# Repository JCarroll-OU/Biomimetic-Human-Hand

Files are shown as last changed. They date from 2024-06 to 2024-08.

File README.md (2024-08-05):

# Biomimetic Human Hand
A mostly 3D-printable 21-DOF biologically inspired robotic human hand prototype.
Joints are actuated via 1mm-diameter 304-Stainless-Steel cable driven by motors in the forearm assembly. These cables are fed through 1mm-ID, 2mm-OD PTFE tubing that runs from the forearm to joints. Additionally, these cables will be driven by N20 motors geared down to 300 RPM.

- **DC Motor Controller PCB** 
  - These PCBs implement a PID control algorithm complete with an auto-tuning feature. Each board can support up to 8 motors, so 4 are required to drive the 21 motors present within this design. Each board is designed to operate at 7-12v.
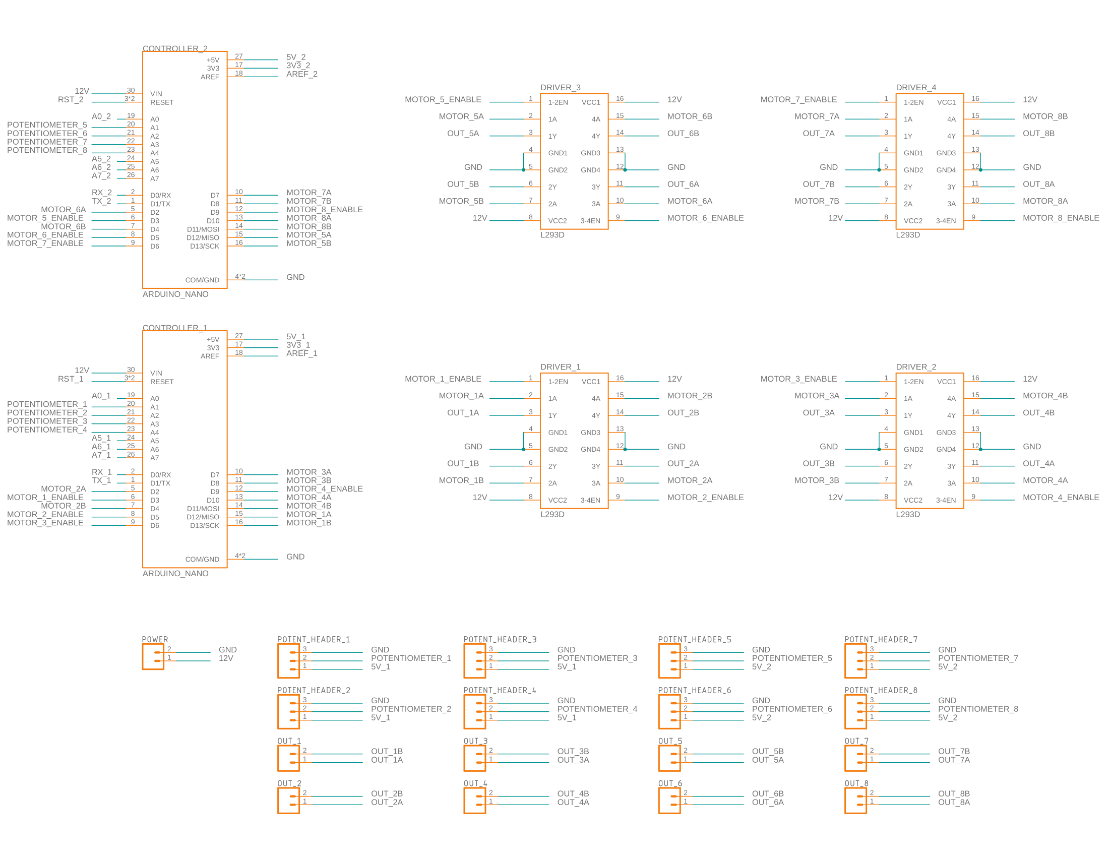
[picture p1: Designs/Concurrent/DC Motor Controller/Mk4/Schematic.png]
Mk. 4 Schematic
  
  - Schematic of Mk. 4 DC Motor Controller PCB. 
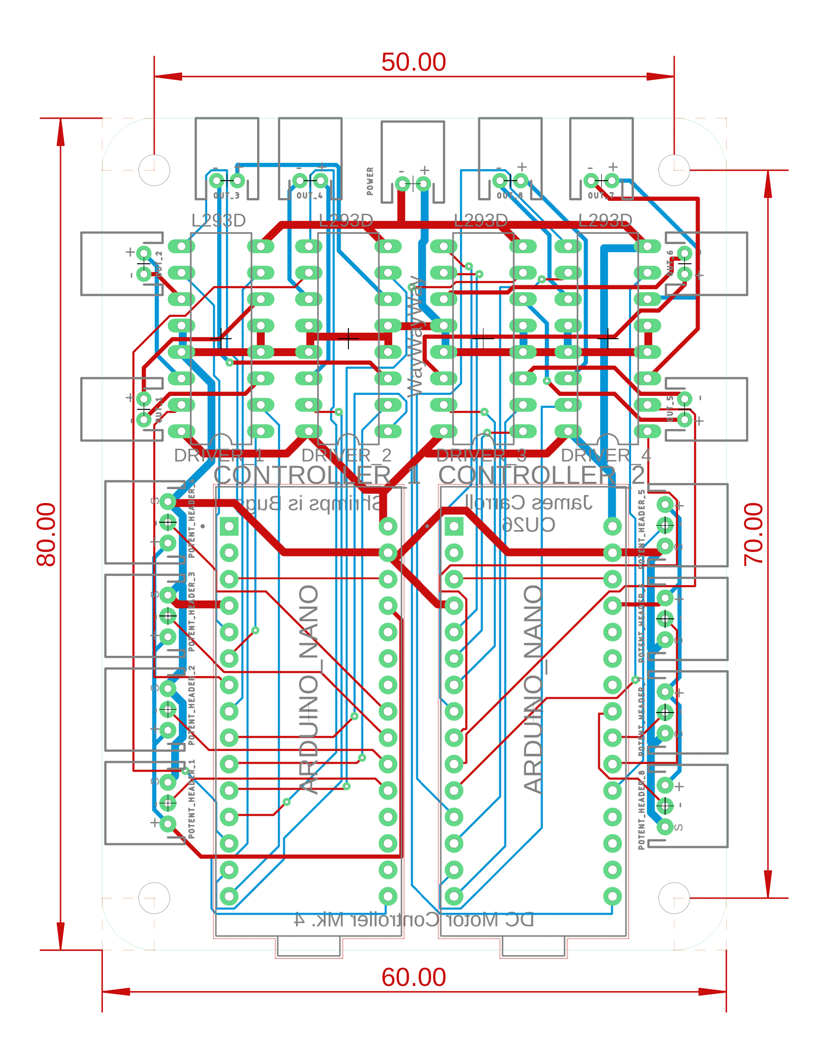
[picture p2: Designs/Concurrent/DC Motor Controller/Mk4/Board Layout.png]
Mk. 4 Board Layout
  
  - PCB Layout and dimensions of Mk. 4 DC Motor Controller PCB. 

- **'Skeletal' System** 
  - Cost was a major design consideration for this prototype. Most parts are designed for 3D-printing (FDM but SLS/SLA is preferrable). Those that are not, are readily available and thus, cheap. 
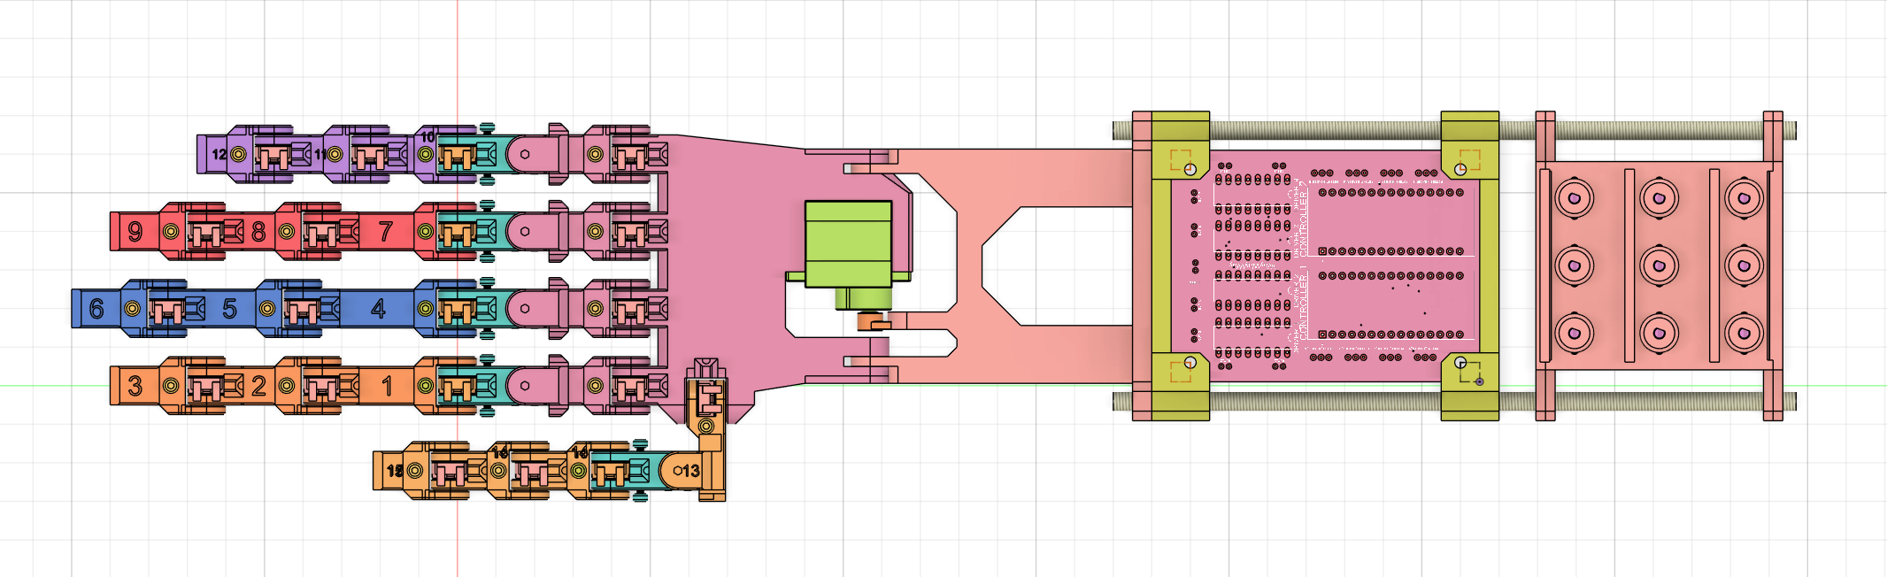
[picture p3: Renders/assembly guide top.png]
WIP: Forearm Assembly, Top
  
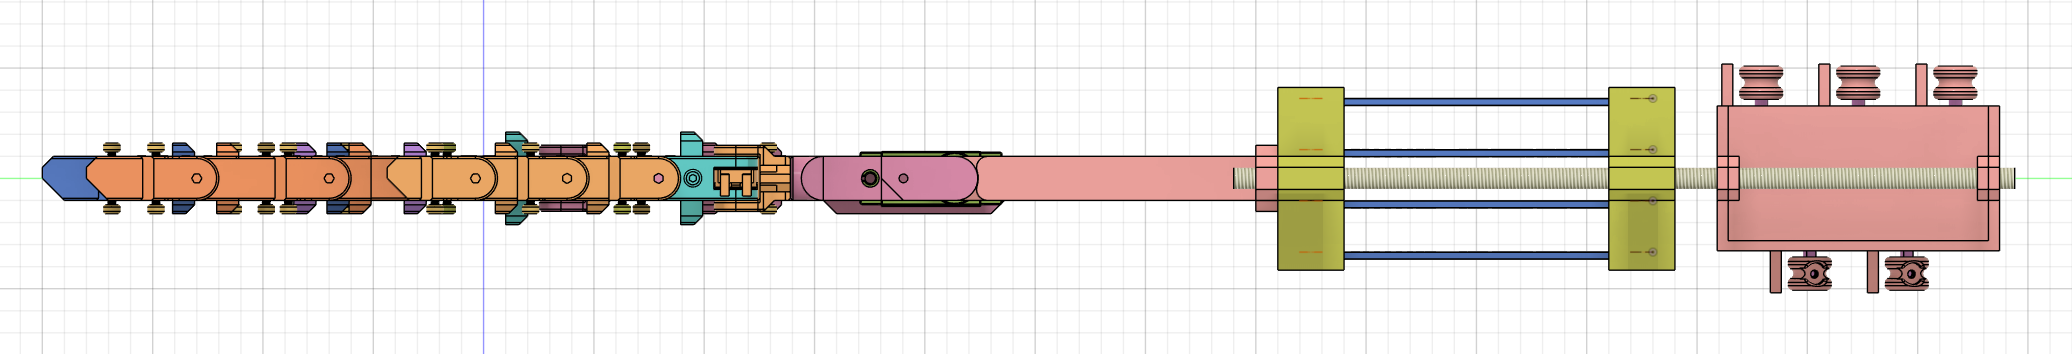
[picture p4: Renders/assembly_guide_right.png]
WIP: Forearm Assembly, Right
  
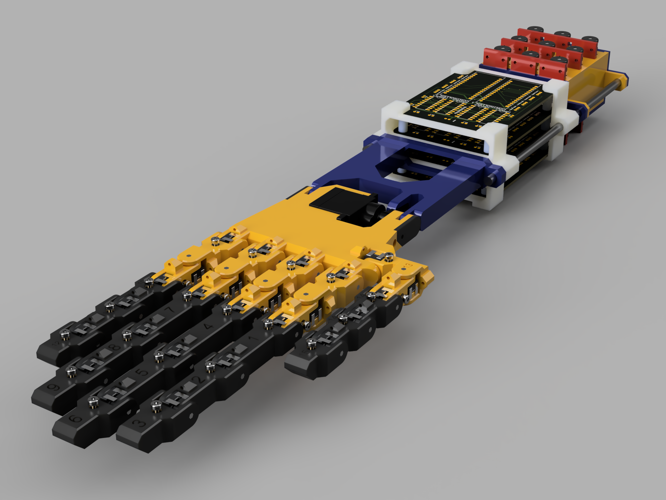
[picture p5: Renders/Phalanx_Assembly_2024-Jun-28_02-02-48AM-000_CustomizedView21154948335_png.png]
WIP: Forearm Assembly, Render
  
  - Finger assemblies in black, palm assembly in yellow, and wrist in blue.
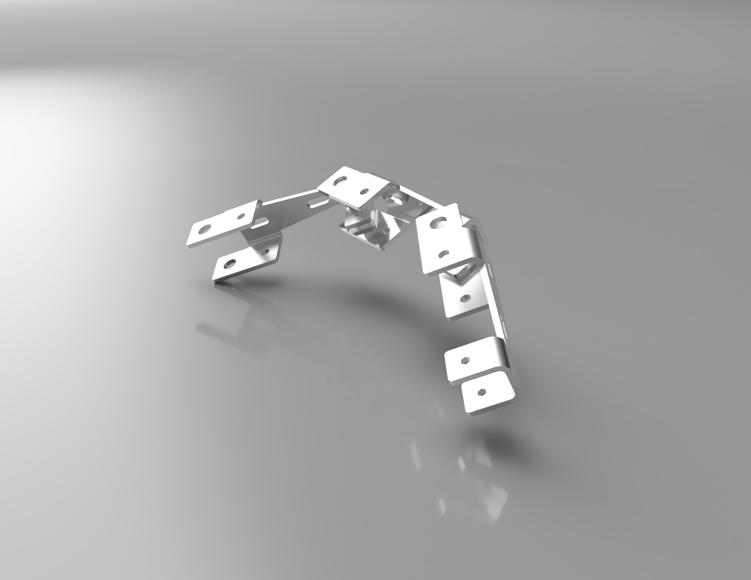
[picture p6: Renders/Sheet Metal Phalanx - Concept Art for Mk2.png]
Concept Art: Production at scale
  
  - Folded sheet metal finger assembly concept art.

  ### This is a work in progress!
  More detailed reports, test results, and notes are available upon request. Contact me or see the license for information regarding the use, reproduction, and distribution of any of the content associated with this project. Thank you!

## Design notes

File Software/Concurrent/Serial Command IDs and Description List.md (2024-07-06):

# Serial Command IDs and descriptions list
  0. SERIAL_CMD_EMPTY
     - Used as part of the handshake protocal. Returns elasped runtime in seconds.
     - Accepts no parameters.
       - Target ID: N/A
       - Param: N/A
     - Example usage:
       - Host: "1 0 0 0.0\n"
         - Controller 1, Command 0, PID 0, 0.0 
       - Client: "13.86\n"
         - Elasped time: 13.86s

  1. SERIAL_CMD_SET_TARGET_ANGLE
     - Sets the 'target angle' variable for the specified PID controller. This is the angle (in degrees) that the PID controller will attempt to move to and hold. 
     - Accepts all parameters
        - Target ID: [1, 4] Int. Values {1, 2, 3, or 4}
          - PID controller to set the target angle of.
        - Param: float [Joint_Range_Min, Joint_Range_Max]
          - New value for the target angle.
     - Example usage:
        - Host: "1 1 2 36.28\n"
          - Controller 1, Command 1, PID 2, 36.28 degrees 
        - Client: "Done\n"

  2. SERIAL_CMD_GET_TARGET_ANGLE
     - Returns the target angle variable for the specified PID controller. 
     - Accepts only the target ID parameter.
        - Target ID: [1, 4] Int. Values {1, 2, 3, or 4}
          - PID controller to get the target angle from.
        - Param: N/A
     - Example usage:
        - Host: "1 2 2 0.0\n"
          - Controller 1, Command 2, PID 2, 0.0 
        - Client: "36.28\n"
          - Target angle: 36.28 degrees

  3. SERIAL_CMD_GET_CURRENT_ANGLE
     - Returns the potentiometer reading (converted to degrees) associated with the specified PID controller.
     - Accepts only the target ID parameter.
        - Target ID: [1, 4] Int. Values {1, 2, 3, or 4}
          - PID controller to get the target angle from.
        - Param: N/A
     - Example usage:
        - Host: "1 3 1 0.0\n"
          - Controller 1, Command 3, PID 1, 0.0 
        - Client: "28.45\n"
          - Current angle: 28.45 degrees

  4. SERIAL_CMD_SET_PID_ENABLE
     - Enables or disables the specified PID controller. Disabling the controller is necessary when manually overriding the motor speed.
     - Accepts all parameters
        - Target ID: [1, 4] Int. Values {1, 2, 3, or 4}
          - PID controller to enable/disable.
        - Param: float, no min/max
          - PID enable state. bool (Param != 0).
     - Example usage:
        - Host: "1 4 3 1.2\n"
          - Controller 1, Command 4, PID 3, 1.2 
        - Client: "Controller_3 enabled\n"
        - Host: "1 4 3 0.0\n"
          - Controller 1, Command 4, PID 3, 0.0
        - Client: "Controller_3 disabled\n"

  5. SERIAL_CMD_GET_PID_ENABLE
     - Returns the state of the specified PID controller.
     - Accepts only the target ID parameter.
        - Target ID: [1, 4] Int. Values {1, 2, 3, or 4}
          - PID controller to get the enable state from.
        - Param: N/A
     - Example usage:
        - Host: "1 5 1 0.0\n"
          - Controller 1, Command 5, PID 1, 0.0 
        - Client: "Enabled\n" or "Disabled\n"

  6. SERIAL_CMD_PID_SET_P
     - Sets the proportional component of the specified PID controller.
     - Accepts all parameters
        - Target ID: [1, 4] Int. Values {1, 2, 3, or 4}
          - PID controller to set the proportional component of.
        - Param: float, no min/max
          - New value for the proportional component.
     - Example usage:
        - Host: "1 6 2 1.86\n"
          - Controller 1, Command 6, PID 2, 1.86 
        - Client: "Done\n"

  7. SERIAL_CMD_PID_GET_P
     - Returns the proportional component of the specified PID controller.
     - Accepts only the target ID parameter.
        - Target ID: [1, 4] Int. Values {1, 2, 3, or 4}
          - PID controller to get the proportional component from.
        - Param: N/A
     - Example usage:
        - Host: "1 7 2 0.0\n"
          - Controller 1, Command 7, PID 2, 0.0 
        - Client: "1.86\n"

  8. SERIAL_CMD_PID_SET_I
     - Sets the integral component of the specified PID controller.
     - Accepts all parameters
        - Target ID: [1, 4] Int. Values {1, 2, 3, or 4}
          - PID controller to set the integral component of.
        - Param: float, no min/max
          - New value for the integral component.
     - Example usage:
        - Host: "1 8 2 1.86\n"
          - Controller 1, Command 8, PID 2, 0.26 
        - Client: "Done\n"

  9. SERIAL_CMD_PID_GET_I
     - Returns the integral component of the specified PID controller.
     - Accepts only the target ID parameter.
        - Target ID: [1, 4] Int. Values {1, 2, 3, or 4}
          - PID controller to get the integral component from.
        - Param: N/A
     - Example usage:
        - Host: "1 9 2 0.0\n"
          - Controller 1, Command 9, PID 2, 0.0 
        - Client: "0.26\n"

  10. SERIAL_CMD_PID_SET_D
      - Sets the derivative component of the specified PID controller.
      - Accepts all parameters
        - Target ID: [1, 4] Int. Values {1, 2, 3, or 4}
          - PID controller to set the derivative component of.
        - Param: float, no min/max
          - New value for the derivative component.
      - Example usage:
        - Host: "1 10 2 0.03\n"
          - Controller 1, Command 8, PID 2, 0.03 
        - Client: "Done\n"

  11. SERIAL_CMD_PID_GET_D
      - Returns the derivative component of the specified PID controller.
      - Accepts only the target ID parameter.
        - Target ID: [1, 4] Int. Values {1, 2, 3, or 4}
          - PID controller to get the derivative component from.
        - Param: N/A
      - Example usage:
        - Host: "1 11 2 0.0\n"
          - Controller 1, Command 11, PID 2, 0.0 
        - Client: "0.03\n"

  12. SERIAL_CMD_SET_ANGLE_CONV_DEG_MIN
      - Sets the minimum bounds for the ADC reading to degrees conversion for the specified PID controller.
      - Accepts all parameters
        - Target ID: [1, 4] Int. Values {1, 2, 3, or 4}
          - PID controller to set the mimimum bounds of.
        - Param: float, no min/max
          - New value for the minimum bounds.
      - Example usage:
        - Host: "1 12 1 24.68\n"
          - Controller 1, Command 12, PID 1, 24.68
        - Client: "Done\n"

  13. SERIAL_CMD_GET_ANGLE_CONV_DEG_MIN
      - Returns the minimum bounds for the ADC reading to degrees conversion for the specified PID controller.
      - Accepts only the target ID parameter.
        - Target ID: [1, 4] Int. Values {1, 2, 3, or 4}
          - PID controller to get the minimum bounds from.
        - Param: N/A
      - Example usage:
        - Host: "1 13 1 0.0\n"
          - Controller 1, Command 13, PID 1, 0.0 
        - Client: "24.68\n"
          
14. SERIAL_CMD_SET_ANGLE_CONV_DEG_MAX
     - Sets the maximum bounds for the ADC reading to degrees conversion for the specified PID controller.
     - Accepts all parameters
        - Target ID: [1, 4] Int. Values {1, 2, 3, or 4}
          - PID controller to set the maximum bounds of.
        - Param: float, no min/max
          - New value for the maximum bounds.
      - Example usage:
        - Host: "1 12 1 76.48\n"
          - Controller 1, Command 14, PID 1, 76.48
        - Client: "Done\n"

  15. SERIAL_CMD_GET_ANGLE_CONV_DEG_MAX
      - Returns the maximum bounds for the ADC reading to degrees conversion for the specified PID controller.
      - Accepts only the target ID parameter.
        - Target ID: [1, 4] Int. Values {1, 2, 3, or 4}
          - PID controller to get the maximum bounds from.
        - Param: N/A
      - Example usage:
        - Host: "1 15 1 0.0\n"
          - Controller 1, Command 15, PID 1, 0.0 
        - Client: "76.48\n"
          
  16. SERIAL_CMD_SET_ANGLE_JOINT_DEG_MIN    
  17. SERIAL_CMD_GET_ANGLE_JOINT_DEG_MIN   
  18. SERIAL_CMD_SET_ANGLE_JOINT_DEG_MAX
  19. SERIAL_CMD_GET_ANGLE_JOINT_DEG_MAX   
          
  20. SERIAL_CMD_SAVE_SETTINGS
  21. SERIAL_CMD_LOAD_SETTINGS

  22. SERIAL_CMD_SET_MOTOR_SPEED
  23. SERIAL_CMD_GET_MOTOR_SPEED
          
  24. SERIAL_CMD_HOMING_SEQUENCE
  25. SERIAL_CMD_PID_AUTOTUNE

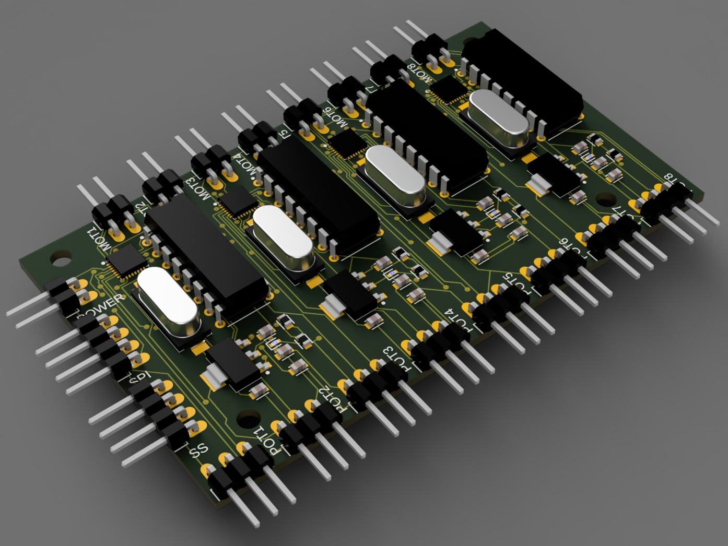
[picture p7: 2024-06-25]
Renders/DC_Motor_Controller_2024-May-17_01-13-07PM-000_CustomizedView9308964263.png

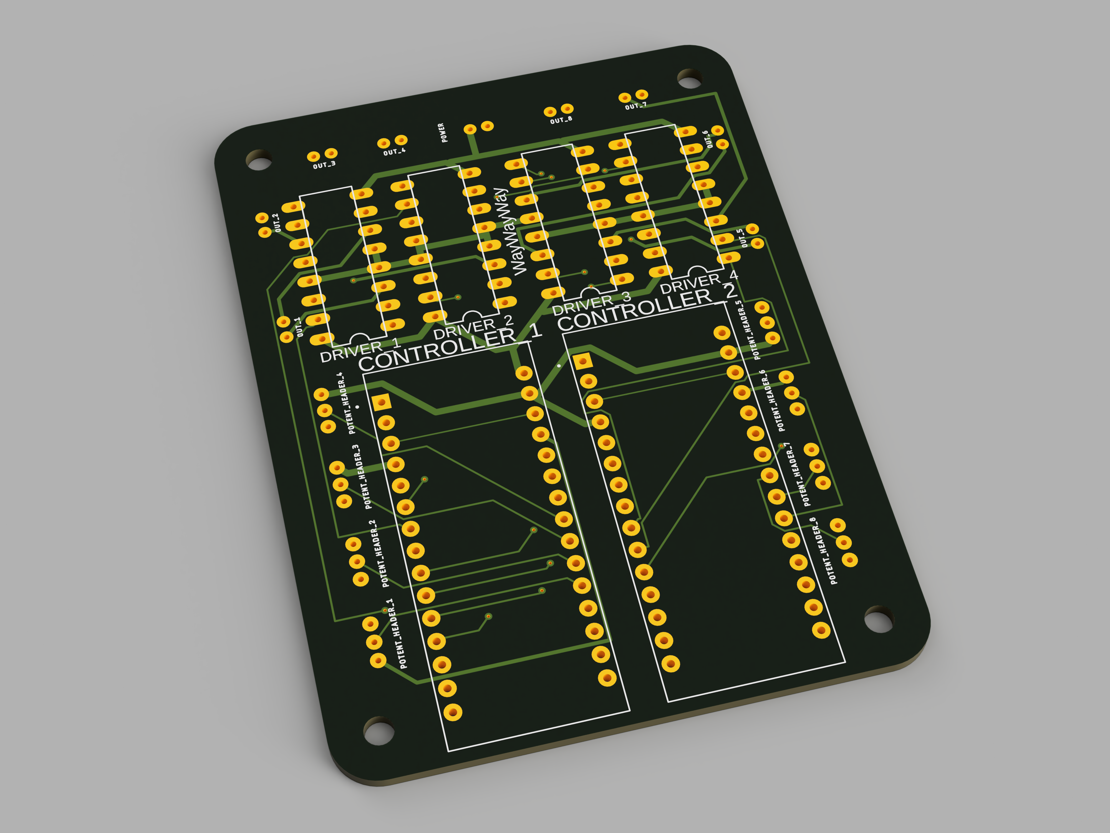
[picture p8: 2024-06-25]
Renders/DC_Motor_Controller_Mk4_2024-Jun-25_07-05-43PM-000_CustomizedView16519912145_png.png

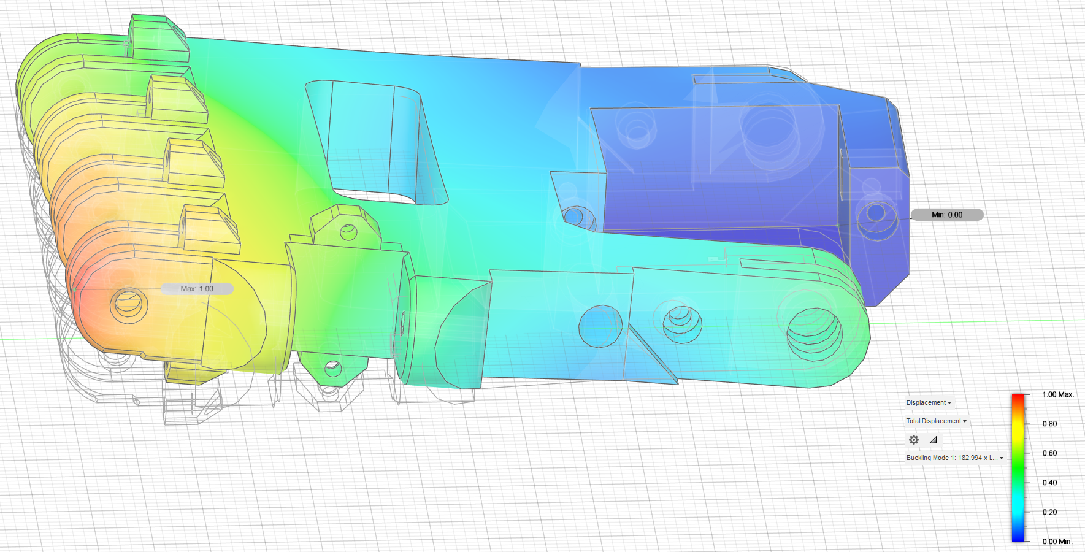
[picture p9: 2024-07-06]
Renders/Screenshot 2024-07-05 212300.png

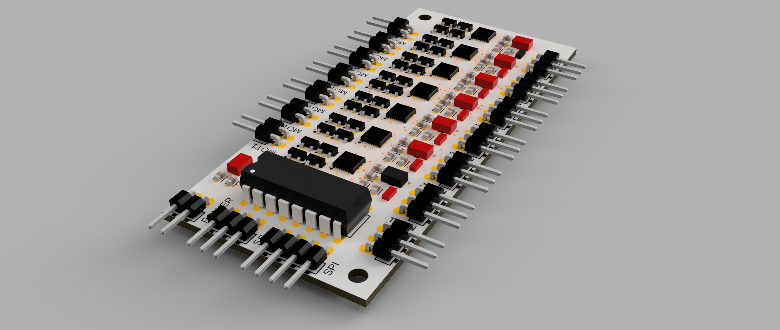
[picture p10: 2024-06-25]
Renders/DC_Motor_Controller_2024-May-16_01-15-25PM-000_CustomizedView20484802570.png

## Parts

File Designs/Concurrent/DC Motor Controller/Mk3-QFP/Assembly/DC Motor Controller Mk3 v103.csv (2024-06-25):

Qty | Value | Device | Package | Parts | Description | CATEGORY | COLOR | DESCRIPTION | MANUFACTURER | MPN | OPERATING_TEMP | OPERATING_TEMPERATURE | PART_STATUS | PITCH | RATING | ROHS_COMPLIANCE | ROHS_COMPLIANT | SERIES | SUB-CATEGORY | SUBCATEGORY | THERMALLOSS | TOLERANCE | TYPE | VALUE | VOLTAGE_RATING
4 | 0.1 Ohms | R_CHIP-0603(1608-METRIC) | RESC1608X60 | R6, R7, R8, R9 | Resistor Fixed - Generic | Resistor |  |  |  |  |  |  |  |  |  |  |  |  | Fixed
6 | 0.1uF | C_CHIP-1206(3216-METRIC) | CAPC3216X135 | C5, C6, C7, C8, C9, C10 | Capacitor - Generic | Capacitor
2 | 10 kOhm | R_CHIP-0603(1608-METRIC) | RESC1608X60 | R4, R5 | Resistor Fixed - Generic | Resistor |  |  |  |  |  |  |  |  |  |  |  |  | Fixed
1 | 100uF | C_CHIP-1206(3216-METRIC) | CAPC3216X135 | C2 | Capacitor - Generic | Capacitor
2 | 10uF | C-POL_TANTALUM-1206(3216-METRIC) | CAPMP3216X180N | C3, C4 | Capacitor Polarised - Generic | Capacitor
1 | 10uF | C_CHIP-1206(3216-METRIC) | CAPC3216X135 | C1 | Capacitor - Generic | Capacitor
3 | 220 Ohm | R_CHIP-0603(1608-METRIC) | RESC1608X60 | R1, R2, R3 | Resistor Fixed - Generic | Resistor |  |  |  |  |  |  |  |  |  |  |  |  | Fixed
2 | ATMEGA328P_TQFP | ATMEGA328P_TQFP | TQFP32-08 | MCU_1, MCU_2 | 8-bit AVR Microcontroller with 32K Bytes In-System Programmable Flash | IC_Embedded |  |  | Microchip | ATmega328P-MMH | -40 to 85 °C |  | Active |  |  |  |  |  | Microcontroller |  |  |  |  | ATMEGA328P
4 | INA180_PINOUTA | INA180_PINOUTA | SOT95P280X145-5N | IC1, IC2, IC3, IC4 | Current-Sense Amplifier | Current Sense Amplifiers |  | Low- and High-Side Voltage Output | Current-Sense Amplifiers | Texas Instruments | Generic | -40°C ~ 125°C |  | Active |  |  |  | ROHS3 Compliant | INA180 | Amplier ICs |  |  |  | Current Sense
4 | L293D | L293D | DIP762W53P254L1969H508Q16B | L293D_1, L293D_2, L293D_3, L293D_4 | L293D H-bridge motor driver | IC_Linear |  | IC MTRDRV BIPLR 4.5-36V 16PWRDIP | STMicroelectronics | L293D | -40°C ~ 150°C |  | Active |  |  |  | ROHS3 Compliant | L293 | Motor Driver |  |  |  | Bipolar
2 | LED_BLUE | CHIP-FLAT-B_0402 | LEDC1005X25N_FLAT-B | D2, D3 |  | LED | BLUE | CHIP LED FLAT |  |  |  |  |  |  |  |  |  |  | CHIP |  |  |  | FLAT_TOP | LED_BLUE
1 | LED_RED | CHIP-FLAT-R_0402 | LEDC1005X25N_FLAT-R | D1 |  | LED | RED | CHIP LED FLAT |  |  |  |  |  |  |  |  |  |  | CHIP |  |  |  | FLAT_TOP | LED_RED
1 | LM7805_SOT223 | LM7805_SOT223 | SOT230P700X170-4 | LM7805 | 5V Voltage Regulator | IC_Logic |  | 5V Voltage Regulator | Generic | Generic |  |  |  |  |  |  |  | LM7805 | Voltage Regulator |  |  |  | 5V
10 | S2B-XH-A | S2B-XH-A | S2B-XH-A | MOT1, MOT2, MOT3, MOT4, MOT5, MOT6, MOT7, MOT8, POWER, SS | CONN HEADER R/A 2POS 2.5MM | Headers |  | Connector Header Through Hole | (2.50mm) | JST Sales America Inc. | S2B-XH-A-1(LF)(SN) |  | -25°C ~ 85°C | Active | (2.50mm) |  | ROHS3 Compliant |  | XH | Rectangular Connectors |  |  |  | Header | Male Pin
8 | S3B-XH-A | S3B-XH-A | S3B-XH-A | POT1, POT2, POT3, POT4, POT5, POT6, POT7, POT8 |  | Header |  | Connector Header Through Hole | (2.50mm) | JST Sales America Inc. | S3B-XH-A(LF)(SN) |  | -25°C ~ 85°C | Active | (2.50mm) |  | ROHS3 Compliant |  | XH |  | Rectangular Connectors |  |  | Header | Male Pin
1 | S4B-XH-A | S4B-XH-A | S4B-XH-A | SPI |  | Header |  | Connector Header Through Hole | (2.50mm) | JST Sales America Inc. | S4B-XH-A(LF)(SN) |  | -25°C ~ 85°C | Active | (2.50mm) |  | ROHS3 Compliant |  | XH |  | Rectangular Connectors |  |  | Header | Male Pin

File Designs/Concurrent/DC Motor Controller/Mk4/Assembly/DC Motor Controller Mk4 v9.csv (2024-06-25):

Qty | Value | Device | Package | Parts | Description | AVAILABILITY | CHECK_PRICES | DESCRIPTION | MF | MP | MPN | OC_FARNELL | OC_NEWARK | PACKAGE | POPULARITY | PRICE | SNAPEDA_LINK
9 |  | CONN_02JST-PTH-2-KIT | JST-2-PTH-KIT | OUT_1, OUT_2, OUT_3, OUT_4, OUT_5, OUT_6, OUT_7, OUT_8, POWER | Multi connection point. Often used as Generic Header-pin footprint for 0.1 inch spaced/style header connections
8 |  | CONN_03JST-PTH-NS | JST-3-PTH-NS | POTENT_HEADER_1, POTENT_HEADER_2, POTENT_HEADER_3, POTENT_HEADER_4, POTENT_HEADER_5, POTENT_HEADER_6, POTENT_HEADER_7, POTENT_HEADER_8 | Multi connection point. Often used as Generic Header-pin footprint for 0.1 inch spaced/style header connections
2 | ARDUINO_NANO | ARDUINO_NANO | SHIELD_ARDUINO_NANO | CONTROLLER_1, CONTROLLER_2 | Arduino Nano, Through Hole Check availability | Not in stock | https://www.snapeda.com/parts/Arduino%20Nano/Arduino/view-part/?ref=eda | Small | complete | and breadboard-friendly board based on the ATmega328 (Arduino Nano 3.x) | Arduino | Arduino Nano |  |  |  | Non-Standard Arduino
4 | L293D | L293D | DIL16 | DRIVER_1, DRIVER_2, DRIVER_3, DRIVER_4 | PUSH-PULL 4 CHANNEL DRIVER |  |  |  |  |  | L293D | 9589619 | 56P8249 |  | 16

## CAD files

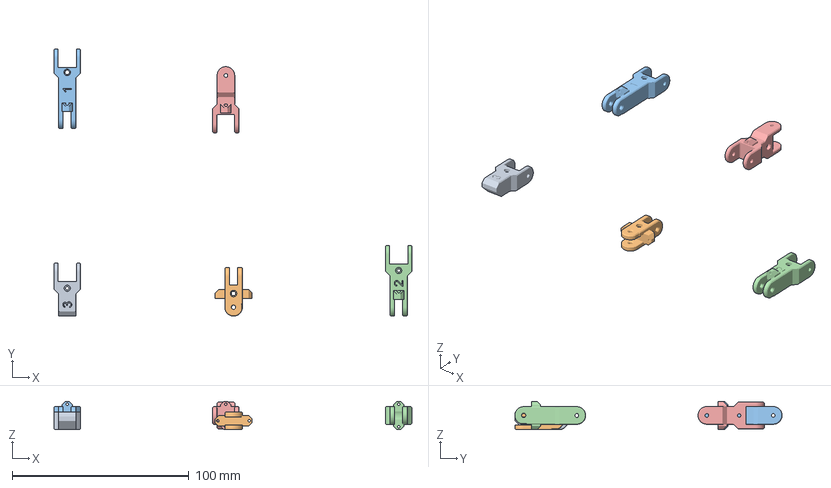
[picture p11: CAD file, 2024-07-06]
Designs/Concurrent/Phalanx Assemblies/Index Finger/Index Finger Assembly.3mf
202.3 x 151.0 x 16.0 mm
Index Distal Phalanx.stl
MCP Joint.stl
Index Proximal Phalanx.stl
Index Middle Phalanx.stl
Index Metacarpus.stl

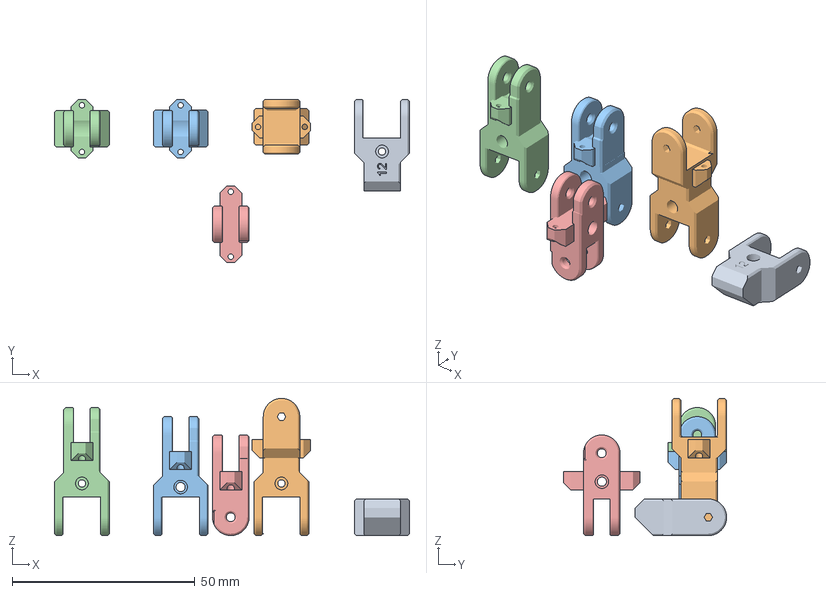
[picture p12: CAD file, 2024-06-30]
Designs/Concurrent/Phalanx Assemblies/Little Finger/Little Finger Assembly.3mf
97.0 x 44.6 x 37.5 mm
Little Distal Phalanx.stl
Little Metacarpus.stl
Little Proximal Phalanx.stl
Little Middle Phalanx.stl
MCP Joint.stl

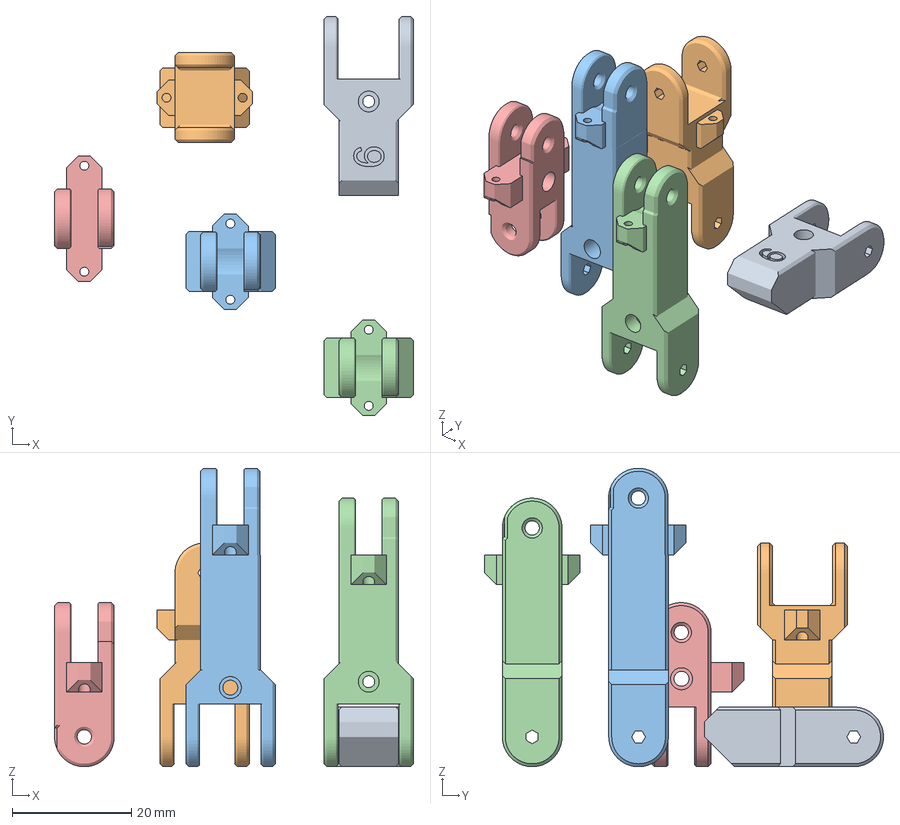
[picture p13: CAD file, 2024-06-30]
Designs/Concurrent/Phalanx Assemblies/Middle Finger/Middle Finger Assembly.3mf
60.1 x 66.9 x 50.0 mm
Middle Distal Phalanx.stl
Middle Metacarpus.stl
Middle Proximal Phalanx.stl
Middle Middle Phalanx.stl
MCP Joint.stl

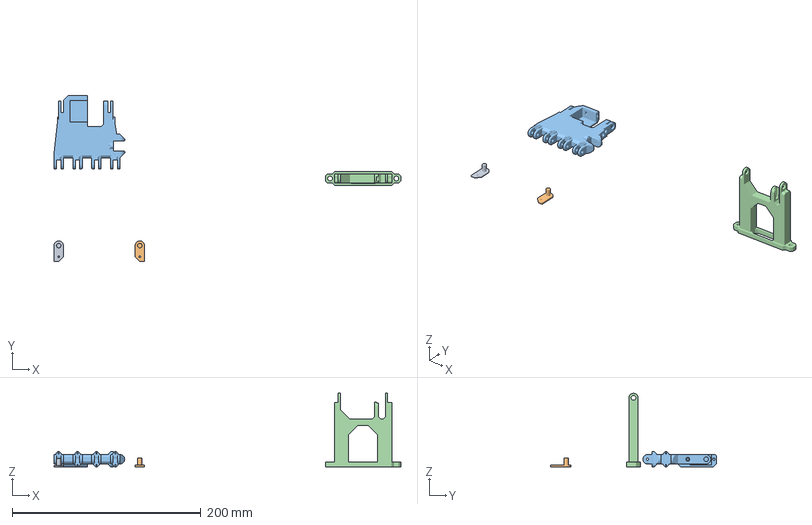
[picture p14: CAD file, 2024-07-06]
Designs/Concurrent/Phalanx Assemblies/Palm and Wrist Assembly/Palm and Wrist Assembly.3mf
367.7 x 175.8 x 78.0 mm
Medial Wrist Axle Cover.stl
Lateral Wrist Axle Cover.stl
Carpus.stl
Wrist Assembly.stl

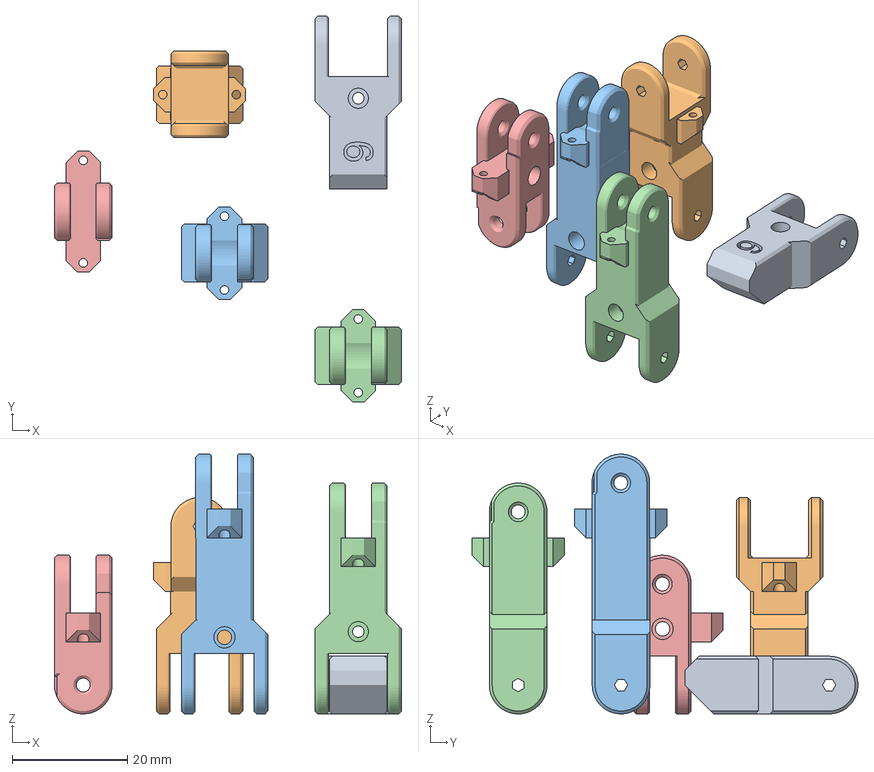
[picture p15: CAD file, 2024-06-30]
Designs/Concurrent/Phalanx Assemblies/Ring Finger/Ring Finger Assembly.3mf
60.1 x 66.9 x 45.0 mm
Ring Distal Phalanx.stl
Ring Metacarpus.stl
Ring Proximal Phalanx.stl
Ring Middle Phalanx.stl
MCP Joint.stl

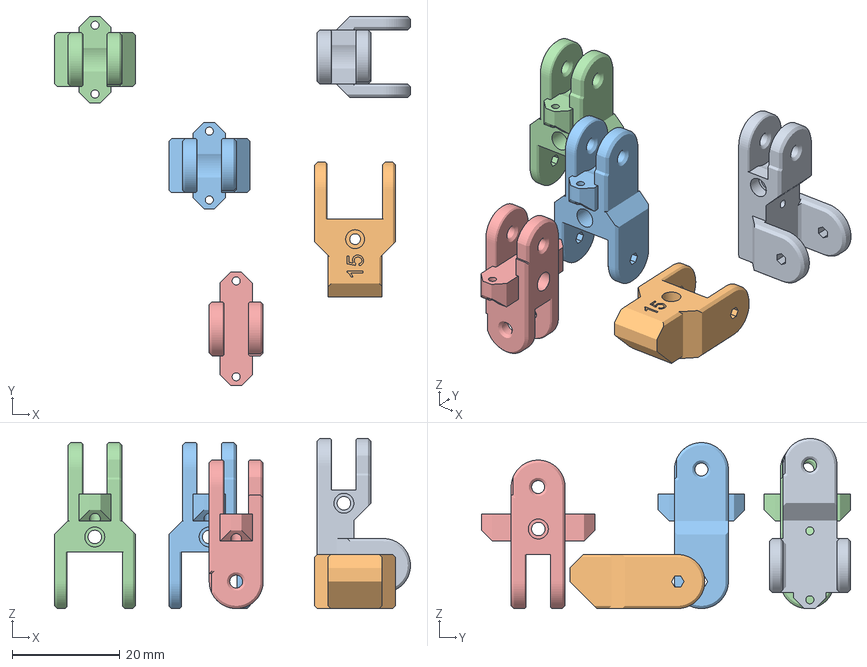
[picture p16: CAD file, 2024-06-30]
Designs/Concurrent/Phalanx Assemblies/Thumb/Thumb Assembly.3mf
65.9 x 68.4 x 31.5 mm
Thumb Metacarpus.stl
Thumb Distal Phalanx.stl
Thumb Middle Phalanx.stl
Thumb Proximal Phalanx.stl
MCP Joint.stl

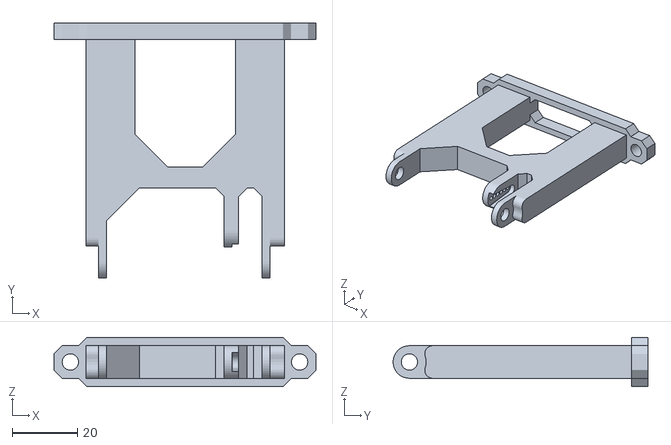
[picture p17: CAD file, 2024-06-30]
Designs/Concurrent/Phalanx Assemblies/Palm and Wrist Assembly/Wrist Assembly.stl
80.2 x 78.0 x 15.0

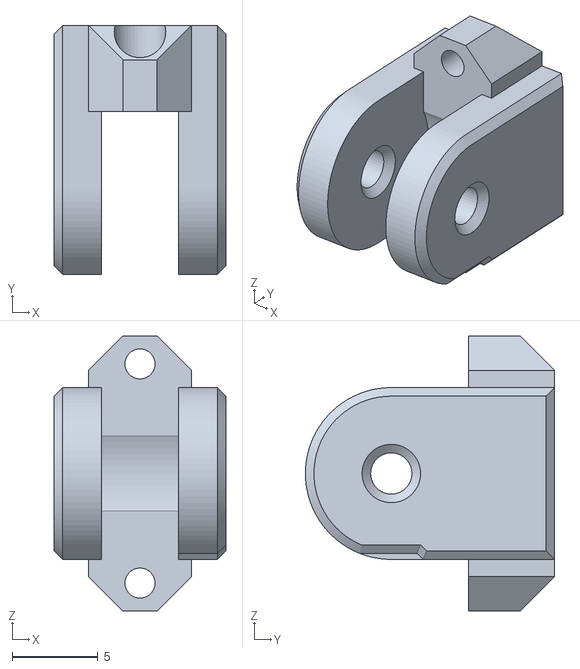
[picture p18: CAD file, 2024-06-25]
Designs/Concurrent/IP Joint/Inner IP Joint.stl
10.0 x 14.5 x 16.0

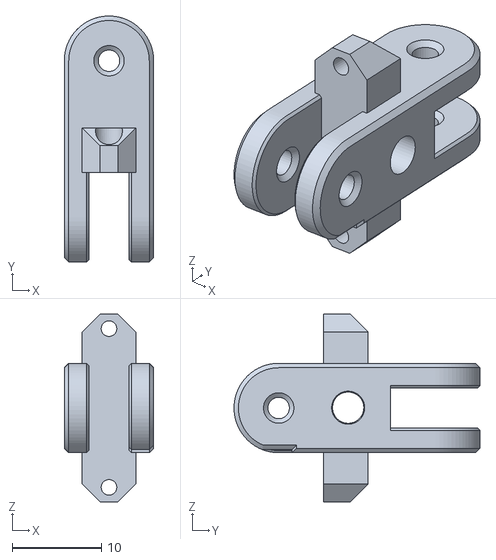
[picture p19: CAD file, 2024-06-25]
Designs/Concurrent/MCP Joint/Inner MCP Joint.stl
10.0 x 27.5 x 21.0

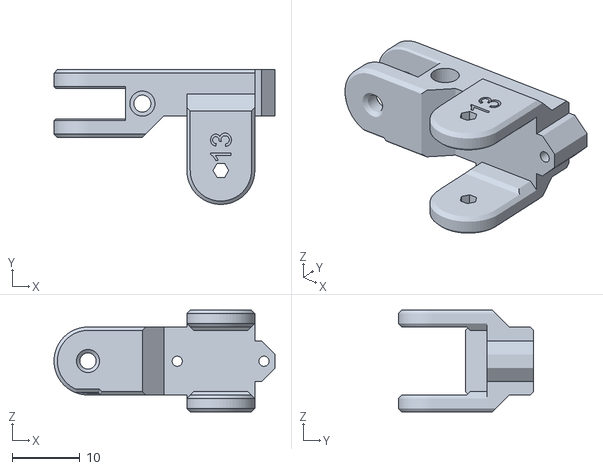
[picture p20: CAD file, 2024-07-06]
Designs/Concurrent/Phalanx Assemblies/Thumb/Thumb Metacarpus.stl
32.5 x 19.8 x 15.0

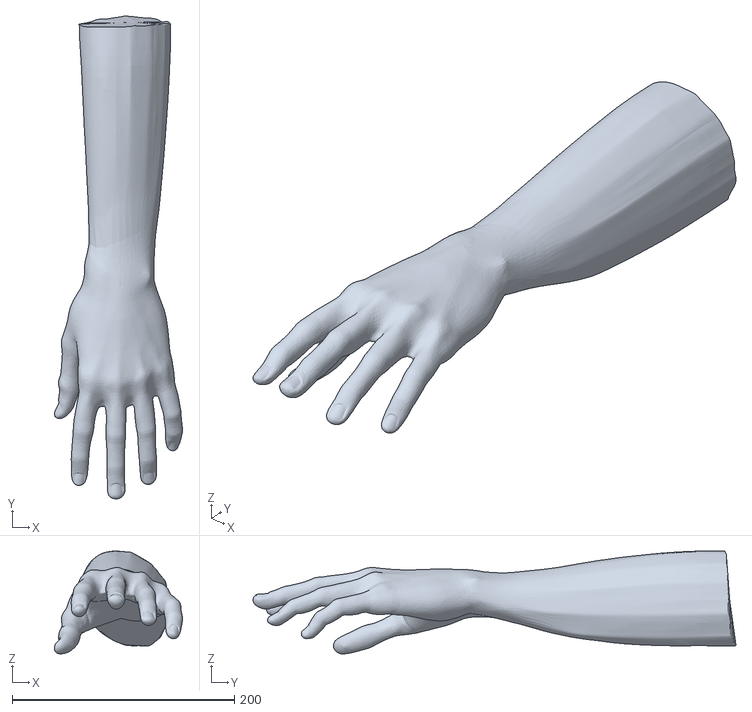
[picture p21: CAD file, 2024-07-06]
Designs/Concurrent/Skin Molding/Negative.stl
115.4 x 434.9 x 92.7

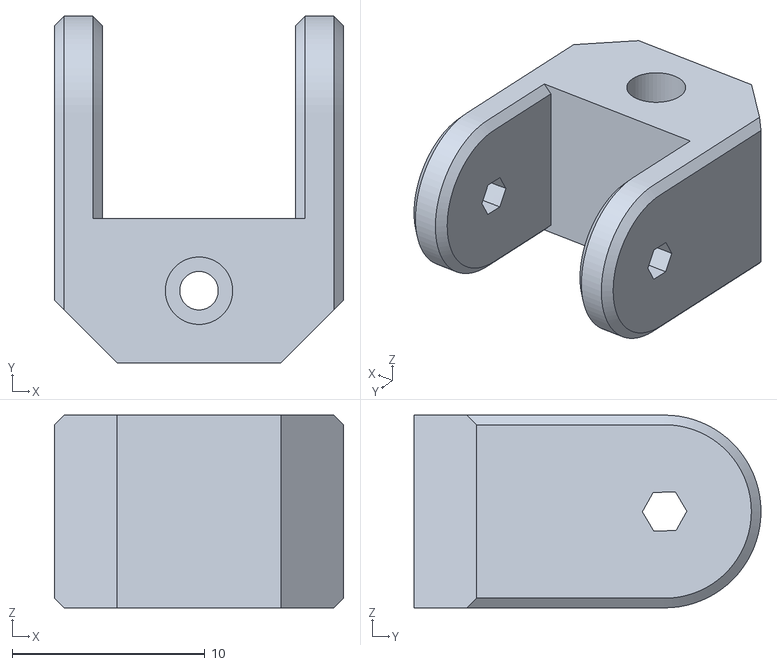
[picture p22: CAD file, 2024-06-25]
Designs/Concurrent/IP Joint/Outer IP Joint.stl
15.0 x 18.0 x 10.0

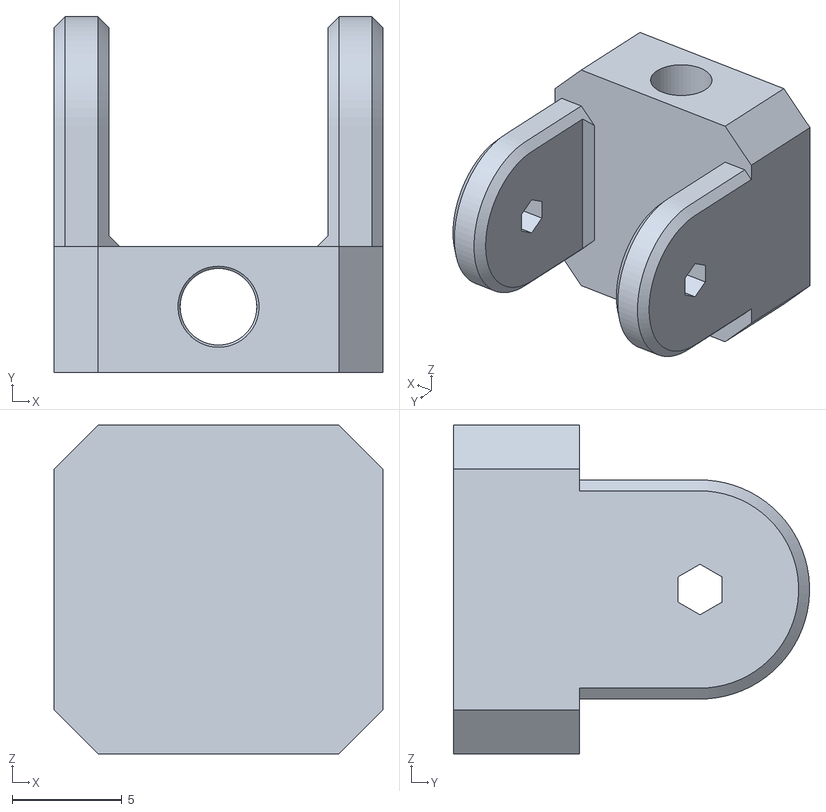
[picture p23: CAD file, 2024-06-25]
Designs/Concurrent/MCP Joint/Fore MCP Joint.stl
15.0 x 16.2 x 15.0

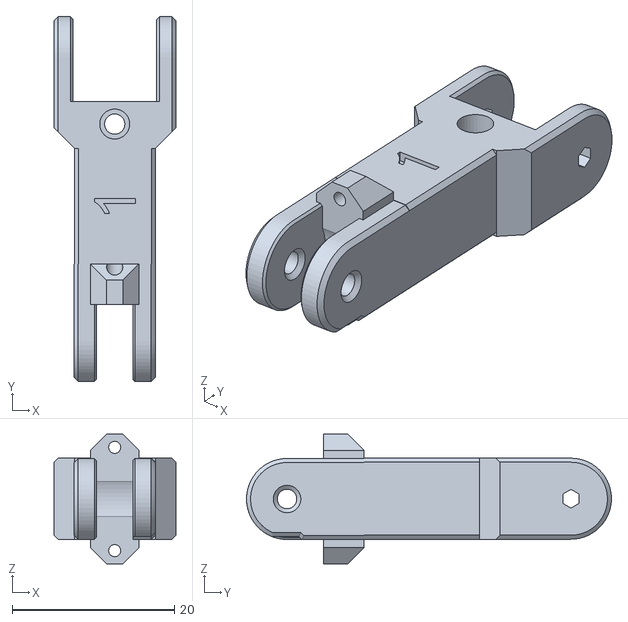
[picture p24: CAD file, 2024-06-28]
Designs/Concurrent/Phalanx Assemblies/Index Finger/Index Proximal Phalanx.stl
15.0 x 45.0 x 16.0

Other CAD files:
Designs/Concurrent/Phalanx Assemblies/Little Finger/Little Distal Phalanx.stl
Designs/Concurrent/Phalanx Assemblies/Middle Finger/Middle Middle Phalanx.stl
Designs/Concurrent/Phalanx Assemblies/Palm and Wrist Assembly/Carpus.stl
Designs/Concurrent/Phalanx Assemblies/Ring Finger/MCP Joint.stl
Designs/Concurrent/MCP Joint/Aft MCP Joint.stl
Designs/Concurrent/Phalanx Assemblies/Index Finger/Index Distal Phalanx.stl
Designs/Concurrent/Phalanx Assemblies/Index Finger/Index Metacarpus.stl
Designs/Concurrent/Phalanx Assemblies/Index Finger/Index Middle Phalanx.stl
Designs/Concurrent/Phalanx Assemblies/Index Finger/MCP Joint.stl
Designs/Concurrent/Phalanx Assemblies/Little Finger/Little Metacarpus.stl
Designs/Concurrent/Phalanx Assemblies/Little Finger/Little Middle Phalanx.stl
Designs/Concurrent/Phalanx Assemblies/Little Finger/Little Proximal Phalanx.stl
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

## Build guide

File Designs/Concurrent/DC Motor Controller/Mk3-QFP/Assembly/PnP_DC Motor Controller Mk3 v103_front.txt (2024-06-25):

C1	3.81	26.29	0.00	10uF	CAPC3216X135
C10	46.11	15.24	0.00	0.1uF	CAPC3216X135
C2	8.89	26.29	180.00	100uF	CAPC3216X135
C3	2.97	43.30	270.00	10uF	CAPMP3216X180N
C4	8.97	43.30	270.00	10uF	CAPMP3216X180N
C5	3.00	50.00	270.00	0.1uF	CAPC3216X135
C6	9.00	50.00	270.00	0.1uF	CAPC3216X135
C7	16.45	15.24	0.00	0.1uF	CAPC3216X135
C8	26.55	15.24	0.00	0.1uF	CAPC3216X135
C9	36.89	15.24	0.00	0.1uF	CAPC3216X135
D1	8.89	14.05	180.00	LED_RED	LEDC1005X25N_FLAT-R
D2	23.59	68.61	180.00	LED_BLUE	LEDC1005X25N_FLAT-B
D3	23.59	45.75	180.00	LED_BLUE	LEDC1005X25N_FLAT-B
IC1	16.26	20.00	270.00	INA180_PINOUTA	SOT95P280X145-5N
IC2	26.36	20.00	270.00	INA180_PINOUTA	SOT95P280X145-5N
IC3	36.70	20.00	270.00	INA180_PINOUTA	SOT95P280X145-5N
IC4	45.92	20.00	270.00	INA180_PINOUTA	SOT95P280X145-5N
LM7805	6.35	19.67	270.00	LM7805_SOT223	SOT230P700X170-4
MCU_1	20.32	59.23	0.00	ATMEGA328P_TQFP	TQFP32-08
MCU_2	20.32	36.37	0.00	ATMEGA328P_TQFP	TQFP32-08
R1	3.81	14.05	180.00	220 Ohm	RESC1608X60
R2	21.05	68.61	180.00	220 Ohm	RESC1608X60
R3	21.05	45.75	180.00	220 Ohm	RESC1608X60
R4	16.85	68.68	270.00	10 kOhm	RESC1608X60
R5	16.99	45.68	270.00	10 kOhm	RESC1608X60
R6	16.45	23.87	0.00	0.1 Ohms	RESC1608X60
R7	26.55	23.87	0.00	0.1 Ohms	RESC1608X60
R8	36.89	23.87	0.00	0.1 Ohms	RESC1608X60
R9	46.11	23.87	0.00	0.1 Ohms	RESC1608X60

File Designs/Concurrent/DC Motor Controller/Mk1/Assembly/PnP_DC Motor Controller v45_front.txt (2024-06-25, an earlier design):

C1	10.00	16.00	90.00	10uF	CAPC1608X85
C10	59.00	16.00	270.00	10uF	CAPC1608X85
C13	79.00	16.00	90.00	10uF	CAPC1608X85
C14	83.00	16.00	270.00	10uF	CAPC1608X85
C2	14.00	16.00	270.00	10uF	CAPC1608X85
C3	33.00	16.00	90.00	10uF	CAPC1608X85
C4	37.00	16.00	270.00	10uF	CAPC1608X85
C9	55.00	16.00	90.00	10uF	CAPC1608X85
D1	12.00	16.00	270.00	LED_RED	LEDC1005X25N_FLAT-R
D2	35.00	16.00	270.00	LED_RED	LEDC1005X25N_FLAT-R
D3	57.00	16.00	90.00	LED_RED	LEDC1005X25N_FLAT-R
D4	81.00	16.00	90.00	LED_RED	LEDC1005X25N_FLAT-R
D5	25.00	13.00	180.00	LED_BLUE	LEDC1005X25N_FLAT-B
D6	48.00	13.00	180.00	LED_BLUE	LEDC1005X25N_FLAT-B
D7	71.00	13.00	180.00	LED_BLUE	LEDC1005X25N_FLAT-B
D8	94.00	13.00	180.00	LED_BLUE	LEDC1005X25N_FLAT-B
IC1	23.00	21.00	0.00	ATMEGA328P	TQFP32-08
IC11	81.00	22.20	90.00	LM7805_SOT223	SOT230P700X170-4
IC13	12.00	22.20	90.00	LM7805_SOT223	SOT230P700X170-4
IC2	46.00	21.00	0.00	ATMEGA328P	TQFP32-08
IC4	35.00	22.20	90.00	LM7805_SOT223	SOT230P700X170-4
IC5	69.00	21.00	0.00	ATMEGA328P	TQFP32-08
IC7	57.00	22.20	90.00	LM7805_SOT223	SOT230P700X170-4
IC8	92.00	21.00	0.00	ATMEGA328P	TQFP32-08
R1	10.00	13.00	180.00	220 Ohm	RESC1608X60
R10	44.00	13.00	0.00	220 Ohm	RESC1608X60
R11	67.00	13.00	0.00	220 Ohm	RESC1608X60
R12	90.00	13.00	0.00	220 Ohm	RESC1608X60
R2	33.00	13.00	180.00	220 Ohm	RESC1608X60
R3	14.00	13.00	180.00	10 kOhm	RESC1608X60
R4	37.00	13.00	180.00	10 kOhm	RESC1608X60
R5	55.00	13.00	180.00	220 Ohm	RESC1608X60
R6	59.00	13.00	180.00	10 kOhm	RESC1608X60
R7	79.00	13.00	0.00	220 Ohm	RESC1608X60
R8	83.00	13.00	180.00	10 kOhm	RESC1608X60
R9	21.00	13.00	0.00	220 Ohm	RESC1608X60

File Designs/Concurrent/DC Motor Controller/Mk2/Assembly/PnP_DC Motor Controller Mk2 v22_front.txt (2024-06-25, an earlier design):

C1	5.20	29.00	0.00	100uF	CAPC3216X135
C2	5.20	17.00	0.00	10uF	CAPC3216X135
C3	17.33	42.00	0.00	10uF	CAPMP3216X180N
C4	17.33	19.00	0.00	10uF	CAPMP3216X180N
D1	10.91	25.00	270.00	LED_RED	LEDC1005X25N_FLAT-R
D2	21.62	60.09	180.00	LED_BLUE	LEDC1005X25N_FLAT-B
D3	21.41	36.91	180.00	LED_BLUE	LEDC1005X25N_FLAT-B
IC1	5.20	23.00	0.00	LM7805_SOT223	SOT230P700X170-4
IC2	19.31	51.00	0.00	ATMEGA328P	TQFP32-08
IC5	19.31	28.00	0.00	ATMEGA328P	TQFP32-08
R1	10.91	21.00	90.00	220 Ohm	RESC1608X60
R2	17.14	60.09	180.00	220 Ohm	RESC1608X60
R3	21.76	41.98	0.00	10 kOhm	RESC1608X60
R4	17.14	36.91	180.00	220 Ohm	RESC1608X60
R5	21.55	18.98	0.00	10 kOhm	RESC1608X60

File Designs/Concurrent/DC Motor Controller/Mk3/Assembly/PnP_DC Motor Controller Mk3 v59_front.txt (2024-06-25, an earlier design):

C1	8.89	34.29	180.00	100uF	CAPC3216X135
C10	15.00	48.00	270.00	0.1uF	CAPC3216X135
C2	3.81	34.29	0.00	10uF	CAPC3216X135
C3	16.45	15.24	0.00	0.1uF	CAPC3216X135
C4	14.97	62.23	270.00	10uF	CAPMP3216X180N
C5	26.55	15.24	0.00	0.1uF	CAPC3216X135
C6	36.89	15.24	0.00	0.1uF	CAPC3216X135
C7	14.97	39.37	270.00	10uF	CAPMP3216X180N
C8	46.11	15.24	0.00	0.1uF	CAPC3216X135
C9	15.00	56.00	270.00	0.1uF	CAPC3216X135
D1	8.89	19.05	180.00	LED_RED	LEDC1005X25N_FLAT-R
D2	23.59	54.61	180.00	LED_BLUE	LEDC1005X25N_FLAT-B
D3	23.59	31.75	180.00	LED_BLUE	LEDC1005X25N_FLAT-B
IC1	16.26	20.00	270.00	INA180_PINOUTA	SOT95P280X145-5N
IC2	26.36	20.00	270.00	INA180_PINOUTA	SOT95P280X145-5N
IC3	36.70	20.00	270.00	INA180_PINOUTA	SOT95P280X145-5N
IC4	45.92	20.00	270.00	INA180_PINOUTA	SOT95P280X145-5N
LM7802	6.35	26.67	270.00	LM7805_SOT223	SOT230P700X170-4
MCU_1	22.32	62.23	0.00	ATMEGA328P	QFN50P500X500X90-33T310N
MCU_2	22.32	39.37	0.00	ATMEGA328P	QFN50P500X500X90-33T310N
R1	3.81	19.05	180.00	220 Ohm	RESC1608X60
R2	21.05	54.61	180.00	220 Ohm	RESC1608X60
R3	22.32	69.85	0.00	10 kOhm	RESC1608X60
R4	26.55	24.13	180.00	0.1 Ohms	RESC1608X60
R5	16.45	24.13	180.00	0.1 Ohms	RESC1608X60
R6	36.89	24.13	180.00	0.1 Ohms	RESC1608X60
R7	22.32	46.99	0.00	10 kOhm	RESC1608X60
R8	21.05	31.75	180.00	220 Ohm	RESC1608X60
R9	46.11	24.13	180.00	0.1 Ohms	RESC1608X60

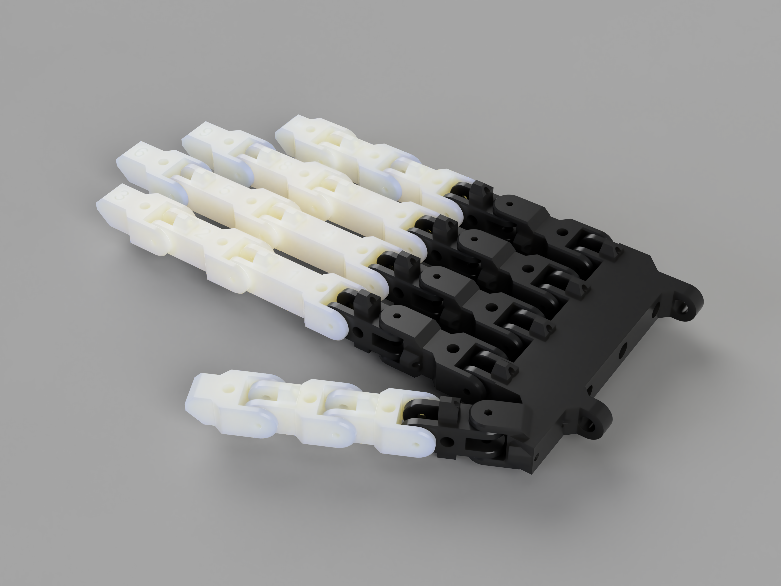
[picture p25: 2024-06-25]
Renders/Phalanx_Assembly_2024-Jun-23_05-39-12PM-000_CustomizedView3688566158_png.png

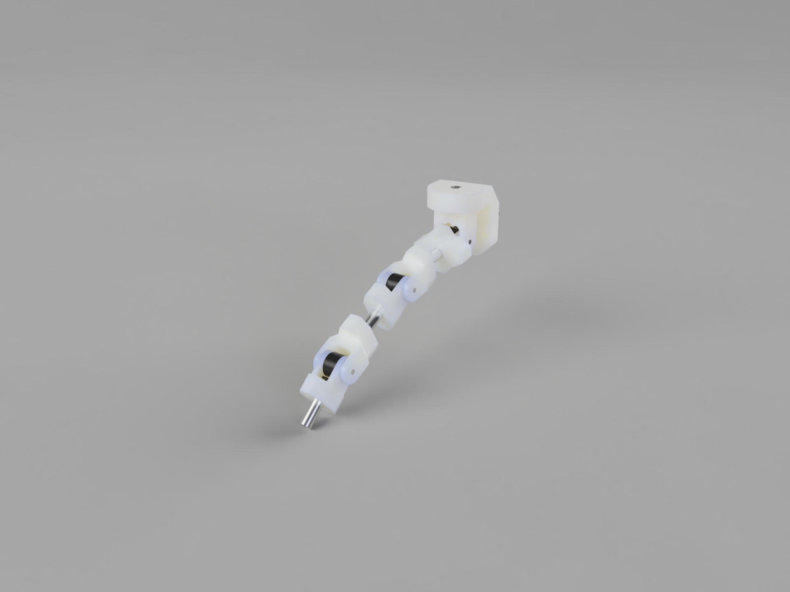
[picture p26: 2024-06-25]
Renders/Phalanx Assembly Mk1.png

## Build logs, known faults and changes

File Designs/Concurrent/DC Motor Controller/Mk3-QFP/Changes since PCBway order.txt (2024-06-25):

Only changes to the silkscreen have been made.
- Fixed value for 5v linear regulator: LM7802 -> LM7805
- Fixed layer for MCU values: Values Top -> Silkscreen Top
- Fixed ammeter capacitor labels on silkscreen: Previously covering small part of each pad
- Repositioned the 'WayWayWay' label to look more centered between the screen and GND label for the potentiometers

Since these are only changes to the silkscreen, and the text on the pads can be scrapped off if it presents an issue, 
a new order will not be made for these board unless they prove to be defective and the circuit itself needs to change.
However, after this many revisions and attempts at getting this to work, this should be a functional board that will
meet the needs of the project, so just move on if it does and keep these updated files since they have the same circuit 
as the working model, just fixed the silkscreen.

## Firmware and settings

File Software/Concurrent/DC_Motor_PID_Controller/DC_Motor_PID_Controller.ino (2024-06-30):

// Pin definitions
#define MOTOR_1_ENABLE 3 // D03 [PWM]
#define MOTOR_1A 12 // D12 (Keep D00 [RX] floating so it does not interfere with programming)
#define MOTOR_1B 13 // D13 (Keep D01 [TX] floating so it does not interfere with programming)

#define MOTOR_2_ENABLE 5 // D05 [PWM]
#define MOTOR_2A 2 // D02
#define MOTOR_2B 4 // D04

#define MOTOR_3_ENABLE 6 // D06 [PWM]
#define MOTOR_3A 7 // D07
#define MOTOR_3B 8 // D08

#define MOTOR_4_ENABLE 9 // D09 [PWM]
#define MOTOR_4A 10 // D10 [This is a PWM pin, however it is not used as one]
#define MOTOR_4B 11 // D11 [This is a PWM pin, however it is not used as one]

#define POTENTIOMETER_1 1 // A01 [ADC]
#define POTENTIOMETER_2 2 // A02 [ADC]
#define POTENTIOMETER_3 3 // A03 [ADC]
#define POTENTIOMETER_4 4 // A04 [ADC]

// Set rate of serial communication
#define BAUD_RATE 19200

// Minimum PWM value for the motors to start spinning
#define MIN_PWM_VAL 115 

// PID values (for array initialization)
#define PID_DEFUALT_KP 1.00
#define PID_DEFUALT_KI 0.25
#define PID_DEFUALT_KD 0.50
#define PID_DEFAULT_VAL 0.0
#define PID_MAX 1.0
#define JOINT_DEFAULT_MIN_DEG 0.0
#define JOINT_DEFAULT_MAX_DEG 90.0
#define PID_DEFAULT_ENABLE_STATE true

// PID Autotune values
#define PID_AUTOTUNE_DEFAULT_GAIN 1e-6
#define PID_AUTOTUNE_OSC_SPD (PID_MAX / 2)
#define PID_AUTOTUNING_DELAY 25

// Error strings, used to reduce the nunber of unique messages in order to save memory
#define ERROR_INVALID_TARGET "Error: Invalid target ID"
#define ERROR_UNKNOWN_COMMAND "Error: Unknown command ID"
#define ERROR_PARAMETER_BOUNDS "Error: Parameter outside acceptable range"
#define ERROR_HOMING_FAILED "Error: Homing sequence failed"
#define ERROR_PID_AUTOTUNE_FAILED "ERROR: PID autotuning sequence failed"
#define COMMAND_COMPLETE "Done" // Sent when no other response is required

// Homing sequence parameters
#define MOTOR_HOMING_SPEED 2.5
#define MOTOR_HOMING_DELAY 5
#define MOTOR_HOMING_TIMEOUT 250 // milliseconds

// Used to save and load data after power is lost
#include <EEPROM.h>

// Identifier used to start serial commands. A command is only followed if the controller ID matches.
#define CONTROLLER_ID 1 // this is so that numerous controllers can share the same serial port

// Values used to track the speed of the motors, used for serial output
float MOTOR_SPEEDS[] = {PID_DEFAULT_ENABLE_STATE, PID_DEFAULT_ENABLE_STATE, PID_DEFAULT_ENABLE_STATE, PID_DEFAULT_ENABLE_STATE};

// PID Enable state, PID Controllers will not update or use their output to set motor speed unless enable is set to true.
bool PID_ENABLE[] = {PID_DEFAULT_ENABLE_STATE, PID_DEFAULT_ENABLE_STATE, PID_DEFAULT_ENABLE_STATE, PID_DEFAULT_ENABLE_STATE};

// PID targets, inputs, and outputs
float PID_TARGETS[] = {PID_DEFAULT_VAL, PID_DEFAULT_VAL, PID_DEFAULT_VAL, PID_DEFAULT_VAL}; // Set points for pid controllers in degrees
float PID_INPUTS[] = {PID_DEFAULT_VAL, PID_DEFAULT_VAL, PID_DEFAULT_VAL, PID_DEFAULT_VAL};  // Potentiometer readings converted to degrees
float PID_OUTPUTS[] = {PID_DEFAULT_VAL, PID_DEFAULT_VAL, PID_DEFAULT_VAL, PID_DEFAULT_VAL}; // Results of the PID controllers.

// P, I, and D values for all PID controllers
float PID_KP[] = {PID_DEFUALT_KP, PID_DEFUALT_KP, PID_DEFUALT_KP, PID_DEFUALT_KP};
int EEPROM_ADDR_PID_KP[] = {0, 4, 8, 12};
float PID_KI[] = {PID_DEFUALT_KI, PID_DEFUALT_KI, PID_DEFUALT_KI, PID_DEFUALT_KI};
int EEPROM_ADDR_PID_KI[] = {16, 20, 24, 28};
float PID_KD[] = {PID_DEFUALT_KD, PID_DEFUALT_KD, PID_DEFUALT_KD, PID_DEFUALT_KD};
int EEPROM_ADDR_PID_KD[] = {32, 36, 40, 44};

// Internal PID variables 
float PID_LastInput[] = {PID_DEFAULT_VAL, PID_DEFAULT_VAL, PID_DEFAULT_VAL, PID_DEFAULT_VAL};
float PID_Integral[] = {PID_DEFAULT_VAL, PID_DEFAULT_VAL, PID_DEFAULT_VAL, PID_DEFAULT_VAL};
unsigned long PID_LastTime[] = {PID_DEFAULT_VAL, PID_DEFAULT_VAL, PID_DEFAULT_VAL, PID_DEFAULT_VAL};
int RAW_POTENTIOMETERS_RDGS[] = {PID_DEFAULT_VAL, PID_DEFAULT_VAL, PID_DEFAULT_VAL, PID_DEFAULT_VAL};
float CONVERSIONS_ADC_MIN_DEG[] = {PID_DEFAULT_VAL, PID_DEFAULT_VAL, PID_DEFAULT_VAL, PID_DEFAULT_VAL};
int EEPROM_ADDR_ADC_MIN_DEG[] = {48, 52, 56, 60};
float CONVERSIONS_ADC_MAX_DEG[] = {JOINT_DEFAULT_MAX_DEG, JOINT_DEFAULT_MAX_DEG, JOINT_DEFAULT_MAX_DEG, JOINT_DEFAULT_MAX_DEG}; // potentiometers have range of [0, 180] degrees
int EEPROM_ADDR_ADC_MAX_DEG[] = {64, 68, 72, 76};
float JOINT_RANGE_MIN_DEG[] = {JOINT_DEFAULT_MIN_DEG, JOINT_DEFAULT_MIN_DEG, JOINT_DEFAULT_MIN_DEG, JOINT_DEFAULT_MIN_DEG};
int EEPROM_ADDR_JOINT_MIN_DEG[] = {80, 84, 88, 92};
float JOINT_RANGE_MAX_DEG[] = {JOINT_DEFAULT_MAX_DEG, JOINT_DEFAULT_MAX_DEG, JOINT_DEFAULT_MAX_DEG, JOINT_DEFAULT_MAX_DEG}; // potentiometers have range of [0, 180] degrees
int EEPROM_ADDR_JOINT_MAX_DEG[] = {96, 100, 104, 108};

// Updates all values corresponding to the PID controller expect for the PID_INPUTS
void PID_Step(int targetID) {
  // Converts the number within the raw potentiometer readings array to degrees and stores it with pid inputs array
  PID_INPUTS[targetID] = ((float)RAW_POTENTIOMETERS_RDGS[targetID] / 1023.0f) * (CONVERSIONS_ADC_MAX_DEG[targetID] - CONVERSIONS_ADC_MIN_DEG[targetID]);
  float timeChange = (float)(millis() - PID_LastTime[targetID]);
  float error = PID_TARGETS[targetID] - PID_INPUTS[targetID];
  PID_Integral[targetID] += (error * timeChange);
  float derivative = (PID_INPUTS[targetID] - PID_LastInput[targetID]) / timeChange;
  PID_OUTPUTS[targetID] = (PID_KP[targetID] * error) + (PID_KI[targetID] * PID_Integral[targetID]) + (PID_KD[targetID] * derivative);
  PID_OUTPUTS[targetID] = constrain(PID_OUTPUTS[targetID], -PID_MAX, PID_MAX);
  PID_LastInput[targetID] = PID_INPUTS[targetID];
  PID_LastTime[targetID] = millis();
}

// Reads the assigned analog pins corresponding to the potentiometer used with each PID controller.
void Update_Potentiometer_Readings() {
  RAW_POTENTIOMETERS_RDGS[0] = analogRead(POTENTIOMETER_1);
  RAW_POTENTIOMETERS_RDGS[1] = analogRead(POTENTIOMETER_2);
  RAW_POTENTIOMETERS_RDGS[2] = analogRead(POTENTIOMETER_3);
  RAW_POTENTIOMETERS_RDGS[3] = analogRead(POTENTIOMETER_4);
}

// Reads the assigned analog pins corresponding to the specified potentiometer used with each PID controller.
void Update_Potentiometer_Readings(int i) {
  switch (i) {
    case 1:
      RAW_POTENTIOMETERS_RDGS[0] = analogRead(POTENTIOMETER_1);
      return;
    case 2:
      RAW_POTENTIOMETERS_RDGS[1] = analogRead(POTENTIOMETER_2);
      return;
    case 3:
      RAW_POTENTIOMETERS_RDGS[2] = analogRead(POTENTIOMETER_3);
      return;
    case 4:
      RAW_POTENTIOMETERS_RDGS[3] = analogRead(POTENTIOMETER_4);
      return;
    default:
      return;
  }
}

/*
  Sets the motor speed of the specified motor.
  @param
    int target accepted values: {1, 2, 3, 4}
        Sets the speed of the motor with an id corresponding to this value.
  @param
    float spd range: [-PID_MAX, PID_MAX]
        Controls both the speed and direction of the motor
*/
void Set_Motor_Speed(int target, float spd) {
  if (abs(spd) > PID_MAX) {
    Serial.println(ERROR_PARAMETER_BOUNDS);
    return;
  }
  int pwmVal = ((abs(spd) / PID_MAX) * (255 - MIN_PWM_VAL)) + MIN_PWM_VAL; // PWM has a range of [0, 255]
  MOTOR_SPEEDS[target - 1] = spd;
  switch (target) {
    case 1: 
      digitalWrite(MOTOR_1A, spd == 0 ? LOW : (spd > 0 ? HIGH : LOW)); // Set the direction of motor 1
      digitalWrite(MOTOR_1B, spd == 0 ? LOW : (spd > 0 ? LOW : HIGH));
      analogWrite(MOTOR_1_ENABLE, pwmVal); // Set the speed for motor 1
      break;
    case 2: 
      digitalWrite(MOTOR_2A, spd == 0 ? LOW : (spd > 0 ? HIGH : LOW)); // Set the direction motor 2
      digitalWrite(MOTOR_2B, spd == 0 ? LOW : (spd > 0 ? LOW : HIGH));
      analogWrite(MOTOR_2_ENABLE, pwmVal); // Set the speed for motor 2
      break;
    case 3: 
      digitalWrite(MOTOR_3A, spd == 0 ? LOW : (spd > 0 ? HIGH : LOW)); // Set the direction motor 3
      digitalWrite(MOTOR_3B, spd == 0 ? LOW : (spd > 0 ? LOW : HIGH));
      analogWrite(MOTOR_3_ENABLE, pwmVal); // Set the speed for motor 3
      break;
    case 4: 
      digitalWrite(MOTOR_4A, spd == 0 ? LOW : (spd > 0 ? HIGH : LOW)); // Set the direction motor 4
      digitalWrite(MOTOR_4B, spd == 0 ? LOW : (spd > 0 ? LOW : HIGH));
      analogWrite(MOTOR_4_ENABLE, pwmVal); // Set the speed for motor 4
      break;
    default:
      Serial.println(ERROR_INVALID_TARGET);
      break;
  }
}

/*
  Reads potentiometers, updates PIDs, and sets motor speed
  @param none
*/
void Update_PID_Controllers() {
  Update_Potentiometer_Readings();
  for (int i = 0; i < 4; i++) {
    if (PID_ENABLE[i]) {
      PID_Step(i);
      Set_Motor_Speed(i + 1, PID_OUTPUTS[i]);
    }
  }
}

/*
  Sets the data direction registers for the necessary pins
  @param none
*/
void Setup_IO() {
  pinMode(MOTOR_1_ENABLE, OUTPUT);
  pinMode(MOTOR_1A, OUTPUT);
  pinMode(MOTOR_1B, OUTPUT);
  pinMode(POTENTIOMETER_1, INPUT);

  pinMode(MOTOR_2_ENABLE, OUTPUT);
  pinMode(MOTOR_2A, OUTPUT);
  pinMode(MOTOR_2B, OUTPUT);
  pinMode(POTENTIOMETER_2, INPUT);

  pinMode(MOTOR_3_ENABLE, OUTPUT);
  pinMode(MOTOR_3A, OUTPUT);
  pinMode(MOTOR_3B, OUTPUT);
  pinMode(POTENTIOMETER_3, INPUT);

  pinMode(MOTOR_4_ENABLE, OUTPUT);
  pinMode(MOTOR_4A, OUTPUT);
  pinMode(MOTOR_4B, OUTPUT);
  pinMode(POTENTIOMETER_4, INPUT);

  pinMode(LED_BUILTIN, OUTPUT);
}

/*
  Writes 4 bytes to the EEPROM starting at the specified location.
  @param
    int location: [0, 1023]
      Location in EEPROM memory (in bytes) to start writing at.
  @param
    float val:
      Value to write. Starting at the specifed location. A float is 4 bytes.

*/
void EEPROM_write_float(int location, float val) {
  byte* b = (byte*)&val;
  EEPROM.update(location + 0, b[0]);
  EEPROM.update(location + 1, b[1]);
  EEPROM.update(location + 2, b[2]);
  EEPROM.update(location + 3, b[3]);
}

/*
  Reads 4 bytes from the EEPROM starting at the specified location.
  @param
    int location: [0, 1023]
      Location in EEPROM memory (in bytes) to start reading at. A float is 4 bytes.
  @return
    float val:
      Value read from EEPROM.

*/
float EEPROM_read_float(int location) {
  byte b[] = { EEPROM.read(location + 0),
               EEPROM.read(location + 1),
               EEPROM.read(location + 2),
               EEPROM.read(location + 3) };
  float result = *((float*)b);
  return isnan(result) ? 0.0f : result;
}

/*
  Calculates the ADC_MIN_DEG and ADC_MAX_DEG values based on potentiometer
  response to driving the motors in either direction for some period of time.
  If the motor is active but no change in the potentiometer reading is
  detected, the current ADC reading is used to calculate the required bounds
  used in the conversion such that they correspond with the specified min. and 
  max joint angles (a measure in degrees).
  Basically, this will automatically calculate the conversion factors used to convert
  the microcontroller's output to a form we can intuitively understand (degrees).
  This conversion is used by the PID controllers and some responses to serial commands. 
  These may be saved using the save and load functions so homing is only required
  when the angle output needs to be corrected. 
  @param
    int target: accepted values = {1, 2, 3, 4}
        Perform the homing sequence on this motor controller.
  @return
    bool homingComplete: true if homing was successfully completed, false otherwise
*/
bool Homing_Sequence(int target) {
  // move the motors forward until position change is no longer registered
  Update_Potentiometer_Readings(target);                              // start by getting the inital potentiometer reading
  int upper_adc_bounds = RAW_POTENTIOMETERS_RDGS[target - 1];
  Set_Motor_Speed(target, MOTOR_HOMING_SPEED);
  delay(MOTOR_HOMING_DELAY);                                          // wait some time before sampling the potentiometer reading
  Update_Potentiometer_Readings(target);                              // sample the potentiometer again so that the values are not equal (unless already stalled)
  upper_adc_bounds = RAW_POTENTIOMETERS_RDGS[target - 1];             // updates bounds after reading the potentiometers. 
  float start_time_ms = millis();                                     // Record the start time
  while (RAW_POTENTIOMETERS_RDGS[target - 1] != upper_adc_bounds) {
    delay(MOTOR_HOMING_DELAY);
    // if the potentiometer values does not stop changing after some period of time, stop the motors and return homing failed.
    if (millis() >= (MOTOR_HOMING_TIMEOUT + start_time_ms)) {
      Set_Motor_Speed(target, 0);
      return false;
    }
    // Update the potentiometer value and track the ADC output
    Update_Potentiometer_Readings(target);
    upper_adc_bounds = RAW_POTENTIOMETERS_RDGS[target - 1];
  } // continously check that joint is moving
  Set_Motor_Speed(target, 0);                                         // Stop the motor

  // move the motors backwards until position change is no longer registered
  Update_Potentiometer_Readings(target);              
  int lower_adc_bounds = RAW_POTENTIOMETERS_RDGS[target - 1];
  Set_Motor_Speed(target, -MOTOR_HOMING_SPEED);                       // move the motor in the opposite direction
  delay(MOTOR_HOMING_DELAY);         
  Update_Potentiometer_Readings(target);                
  lower_adc_bounds = RAW_POTENTIOMETERS_RDGS[target - 1];
  start_time_ms = millis();                                           // Update the start time
  while (RAW_POTENTIOMETERS_RDGS[target - 1] != lower_adc_bounds) {
    delay(MOTOR_HOMING_DELAY);
    // if the potentiometer values does not stop changing after some period of time, stop the motors and return homing failed.
    if (millis() >= (MOTOR_HOMING_TIMEOUT + start_time_ms)) {
      Set_Motor_Speed(target, 0);
      return false;
    }
    // Update the potentiometer value and track the ADC output
    Update_Potentiometer_Readings(target);
    lower_adc_bounds = RAW_POTENTIOMETERS_RDGS[target - 1];
  }
  Set_Motor_Speed(target, 0);                                         // Stop the motor

  // check that the following steps will result in a defined value, if not return homing failed
  if ((lower_adc_bounds - upper_adc_bounds) == 0 || (JOINT_RANGE_MIN_DEG[target - 1] - JOINT_RANGE_MAX_DEG[target - 1]) == 0) return false;
  else { // if either of the values above are zero, then the following calculation cannot be made (undefined)
    /* Calculate the required upper and lower bounds to output JOINT_MIN_DEG to JOINT_MAX_DEG degrees given adc readings
        deg_min is the angle (in degrees) that corresponds to an ADC reading of 0
                  (adc_min * joint_max) - (joint_min * adc_max)
        deg_min = ---------------------------------------------
                              adc_min - adc_max

        deg_max is the angle (in degrees) that corresponds to an ADC reading of 1023
                  (adc_min * joint_max) - (joint_min * [adc_max - 1023]) - (1023 * joint_max)
        deg_max = ---------------------------------------------------------------------------
                                              adc_min - adc_max
    */
    CONVERSIONS_ADC_MIN_DEG[target - 1] = ((lower_adc_bounds * JOINT_RANGE_MAX_DEG[target - 1]) - (JOINT_RANGE_MIN_DEG[target - 1] * upper_adc_bounds)) / (lower_adc_bounds - upper_adc_bounds); 
    CONVERSIONS_ADC_MAX_DEG[target - 1] = ((lower_adc_bounds * JOINT_RANGE_MAX_DEG[target - 1]) - (JOINT_RANGE_MIN_DEG[target - 1] * (upper_adc_bounds - 1023)) - (JOINT_RANGE_MAX_DEG[target - 1] * 1023)) / (lower_adc_bounds - upper_adc_bounds);
    return true;
  }
}

/*
  Ziegler-Nicholas PID auto-tuning method. Calculates the ultimate gain 'Ku' and 'Tu'
  after oscillating the motors and monitoring the response. Returns true if tuning is
  successful, otherwise returns false.
  @param
    int target: accepted values = {1, 2, 3, 4}
        Perform the auto-tuning sequence on this PID controller.
  @param
    float duration: All positive values are acceptable.
        Time (in seconds) to oscillate the motor for before performing any calculations.
*/
bool PID_Autotune(int target, float duration) {
  float minInput = PID_AUTOTUNE_DEFAULT_GAIN;
  float maxInput = -PID_AUTOTUNE_DEFAULT_GAIN;
  float Ku = PID_DEFAULT_VAL;
  float Tu = PID_DEFAULT_VAL;
  unsigned long startTime = millis();

  // Set the PID target to the current angle. 
  // It is recommended that you set the PID target to the mid-point of the range of motion as demonstrated below:
  //  ((JOINT_RANGE_MAX_DEG[target - 1] - JOINT_RANGE_MIN_DEG[target - 1]) / 2) + JOINT_RANGE_MIN_DEG[target - 1];
  // Then allow time for the PID controller to acheieve that position. Then run this function. This will help avoid
  // the oscillations from driving joints outside their range of motion. 
  PID_TARGETS[target - 1] = PID_INPUTS[target - 1];
  // Drive the motor forward to begin oscillating
  Set_Motor_Speed(target, PID_AUTOTUNE_OSC_SPD);

  float deltaTime = millis() - startTime;
  while ((deltaTime / 1000.0f) < duration) {
    deltaTime = millis() - startTime;

    // Find min and max input values to determine oscillation
    if (PID_INPUTS[target - 1] < minInput) minInput = PID_INPUTS[target - 1];
    if (PID_INPUTS[target - 1] > maxInput) maxInput = PID_INPUTS[target - 1];

    // Toggle the motor direction to induce oscillations
    Set_Motor_Speed(target, -MOTOR_SPEEDS[target - 1]);

    // Check if we have a complete oscillation
    if ((PID_INPUTS[target - 1] > PID_TARGETS[target - 1] && PID_LastInput[target - 1] <= PID_TARGETS[target - 1]) ||
        (PID_INPUTS[target - 1] < PID_TARGETS[target - 1] && PID_LastInput[target - 1] >= PID_TARGETS[target - 1])) {
      double oscillationTime = deltaTime / 1000.0; // Oscillation period in seconds
      if (Tu == 0)
        Tu = oscillationTime;
      else
        Tu = (Tu + oscillationTime) / 2.0; // Average period
      startTime = millis();
      minInput = PID_AUTOTUNE_DEFAULT_GAIN;
      maxInput = -PID_AUTOTUNE_DEFAULT_GAIN;
    }

    // Wait some time so the motors have time to move past their target
    delay(PID_AUTOTUNING_DELAY);
  }

  Ku = PID_MAX * ((255 - MIN_PWM_VAL) / (maxInput - minInput));
  PID_KP[target - 1] = 0.6 * Ku; // In accordance with the Ziegler-Nicholas tuning method, KP is approximately 60% of Ku.
  PID_KI[target - 1] = 2 * PID_KP[target - 1] / Tu; // KI = (2 * KP) / Tu
  PID_KD[target - 1] = PID_KP[target - 1] * Tu / 8; // KD = (KP * Tu) / 8
  return true;
}

/*
  Saves the kP, kI, kD, and the conversion factors for each PID controller to the EEPROM.
*/
void Save_Settings() {
  for (int i = 0; i < 4; i++) { 
      EEPROM_write_float(EEPROM_ADDR_PID_KP[i], PID_KP[i]);
      EEPROM_write_float(EEPROM_ADDR_PID_KI[i], PID_KI[i]);
      EEPROM_write_float(EEPROM_ADDR_PID_KD[i], PID_KD[i]);
      EEPROM_write_float(EEPROM_ADDR_ADC_MIN_DEG[i], CONVERSIONS_ADC_MIN_DEG[i]);
      EEPROM_write_float(EEPROM_ADDR_ADC_MAX_DEG[i], CONVERSIONS_ADC_MAX_DEG[i]);
      EEPROM_write_float(EEPROM_ADDR_JOINT_MIN_DEG[i], JOINT_RANGE_MIN_DEG[i]);
      EEPROM_write_float(EEPROM_ADDR_JOINT_MAX_DEG[i], JOINT_RANGE_MAX_DEG[i]);
    }
}

/*
  Loads the kP, kI, kD, and the conversion factors for each PID controller from the EEPROM.
*/
void Load_Settings() {
  for (int i = 0; i < 4; i++) { 
      PID_KP[i] = EEPROM_read_float(EEPROM_ADDR_PID_KP[i]);
      PID_KI[i] = EEPROM_read_float(EEPROM_ADDR_PID_KI[i]);
      PID_KD[i] = EEPROM_read_float(EEPROM_ADDR_PID_KD[i]);
      CONVERSIONS_ADC_MIN_DEG[i] = EEPROM_read_float(EEPROM_ADDR_ADC_MIN_DEG[i]);
      CONVERSIONS_ADC_MAX_DEG[i] = EEPROM_read_float(EEPROM_ADDR_ADC_MAX_DEG[i]);
      JOINT_RANGE_MIN_DEG[i] = EEPROM_read_float(EEPROM_ADDR_JOINT_MIN_DEG[i]);
      JOINT_RANGE_MAX_DEG[i] = EEPROM_read_float(EEPROM_ADDR_JOINT_MAX_DEG[i]);
    }
}

void SERIAL_CMD_EMPTY() {
  // respond to handshake request with current runtime in seconds
  Serial.println(((float)millis() / 1000.0f)); 
}

void SERIAL_CMD_SET_TARGET_ANGLE(int target, float param) {
  if (param > JOINT_RANGE_MAX_DEG[target - 1] || param < JOINT_RANGE_MIN_DEG[target - 1]) {
    Serial.println(ERROR_PARAMETER_BOUNDS);
    return;
  }
  PID_TARGETS[target - 1] = param;
  Serial.println(COMMAND_COMPLETE);
}

void SERIAL_CMD_GET_TARGET_ANGLE(int target) {
  Serial.println(String(PID_TARGETS[target - 1]));
}

void SERIAL_CMD_GET_CURRENT_ANGLE(int target) {
  Serial.println(String(PID_INPUTS[target - 1]));
}

void SERIAL_CMD_SET_PID_ENABLE(int target, float param) {
  PID_ENABLE[target - 1] = param != 0;
  String header = "Controller_" + String(target) + " disabled";
  if (PID_ENABLE[target - 1]) // there are better ways of doing this, but they all give some kind of error
    header = "Controller_" + String(target) + " enabled";
  Serial.println(header);
}

void SERIAL_CMD_GET_PID_ENABLE(int target) {
  String resp = "Disabled";
  if (PID_ENABLE[target - 1]) // there are better ways of doing this, but they all give some kind of error
    resp = "Enabled";
  Serial.println(resp);
}

void SERIAL_CMD_PID_SET_P(int target, float param) {
  PID_KP[target - 1] = param;
  Serial.println(COMMAND_COMPLETE);
}

void SERIAL_CMD_PID_GET_P(int target) {
  Serial.println(PID_KP[target - 1]);
}

void SERIAL_CMD_PID_SET_I(int target, float param) {
  PID_KI[target - 1] = param;
  Serial.println(COMMAND_COMPLETE);
}

void SERIAL_CMD_PID_GET_I(int target) {
  Serial.println(PID_KI[target - 1]);
}

void SERIAL_CMD_PID_SET_D(int target, float param) {
  PID_KD[target - 1] = param;
  Serial.println(COMMAND_COMPLETE);
}
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
void loop() {
  Process_Serial();

  digitalWrite(LED_BUILTIN, HIGH);
  delay(25); // this is only here for debug purposes, PIDs could be updated much quicker without this

  // Reads the potentiometers and converts to degrees, then updates the PID controllers, and finally, sets the motor speeds.
  Update_PID_Controllers();

  digitalWrite(LED_BUILTIN, LOW);
  delay(25);
}

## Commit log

2024-06-25 Initial Commit
    Includes a variety of project files, including but not limited to the DC motor controller PCB, 'skeleton' of the robotic hand, and software for controlling the robot.
    [Aft MCP Joint.stl, Carpus.stl, DC Motor Controller Mk2 v22.csv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]
2024-06-25 Restructured files
    Moved all active design folders to 'Concurrent Designs' folder. Added new folder for software, to be populated with later commits (files originate from a different device).
    [Aft MCP Joint.stl, Carpus.stl, Fore MCP Joint.stl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]
2024-06-25 Restructured files and added some things.
    Added render of Mk. 4 DC Motor Controller. Added reasons for deprecation to deprecated project folders. Moved designs into a more logical structure. Added software folder structure.
    [Aft MCP Joint.stl, Carpus.stl, DC Motor Controller Mk2 v22.csv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]
2024-06-27 Updated PID controller code
    Changed homing sequence timeout process, restructured command processor, added min. PWM value for more precise motor control, and restructured the command processor. Reduce program storage usage from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
2024-06-27 Added PID Auto-tuning
    Implemented the Ziegler-Nichols PID auto-tuning method.
2024-06-28 Updated STL files
    Exported STLs for newest version of design
    [Carpus.stl, Index Distal Phalanx.stl, Index Metacarpus.stl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]
2024-06-29 Tested PID output and tuning
    Passed. However further testing is required with complete assembly, tuning output is NaN if motor is not coupled to potentiometer.
2024-06-30 Create OrcaSlicer Settings.3mf
    [OrcaSlicer Settings.3mf]
2024-06-30 Removed ocra config and gocde
    gcode was specific to my printer and is not required in this repository
    [OrcaSlicer Settings.3mf]
2024-06-30 Updated design
    Continued work on wrist assembly and improved FDM print reliability.
    [Carpus.stl, Index Finger Assembly.3mf, Lateral Wrist Axle Cover.stl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]
2024-06-30 Updated forearm assembly
    [Palm and Wrist Assembly.3mf, Wrist Assembly.stl]
2024-07-06 Updated design and documentation
    Added command list descriptions for the first 16 commands (of 25) and updated the 'carpus' and 'thumb metacarpus' parts to better utilize heat set threaded inserts.
    [Carpus.stl, Index Finger Assembly.3mf, Negative.stl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]
